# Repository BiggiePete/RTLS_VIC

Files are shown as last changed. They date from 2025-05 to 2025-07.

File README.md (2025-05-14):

# RTLS_VIC


Return to launch senior design kicad hardware repo for Vehicle In-flight Controller 

## Visit HTML BOM
https://biggiepete.github.io/RTLS_VIC/

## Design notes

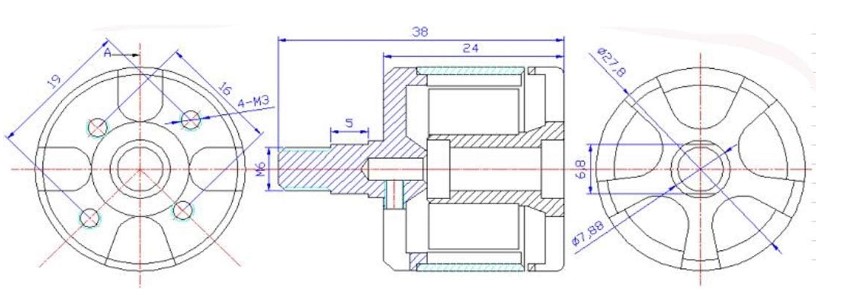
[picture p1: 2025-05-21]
motorSizing.jpg

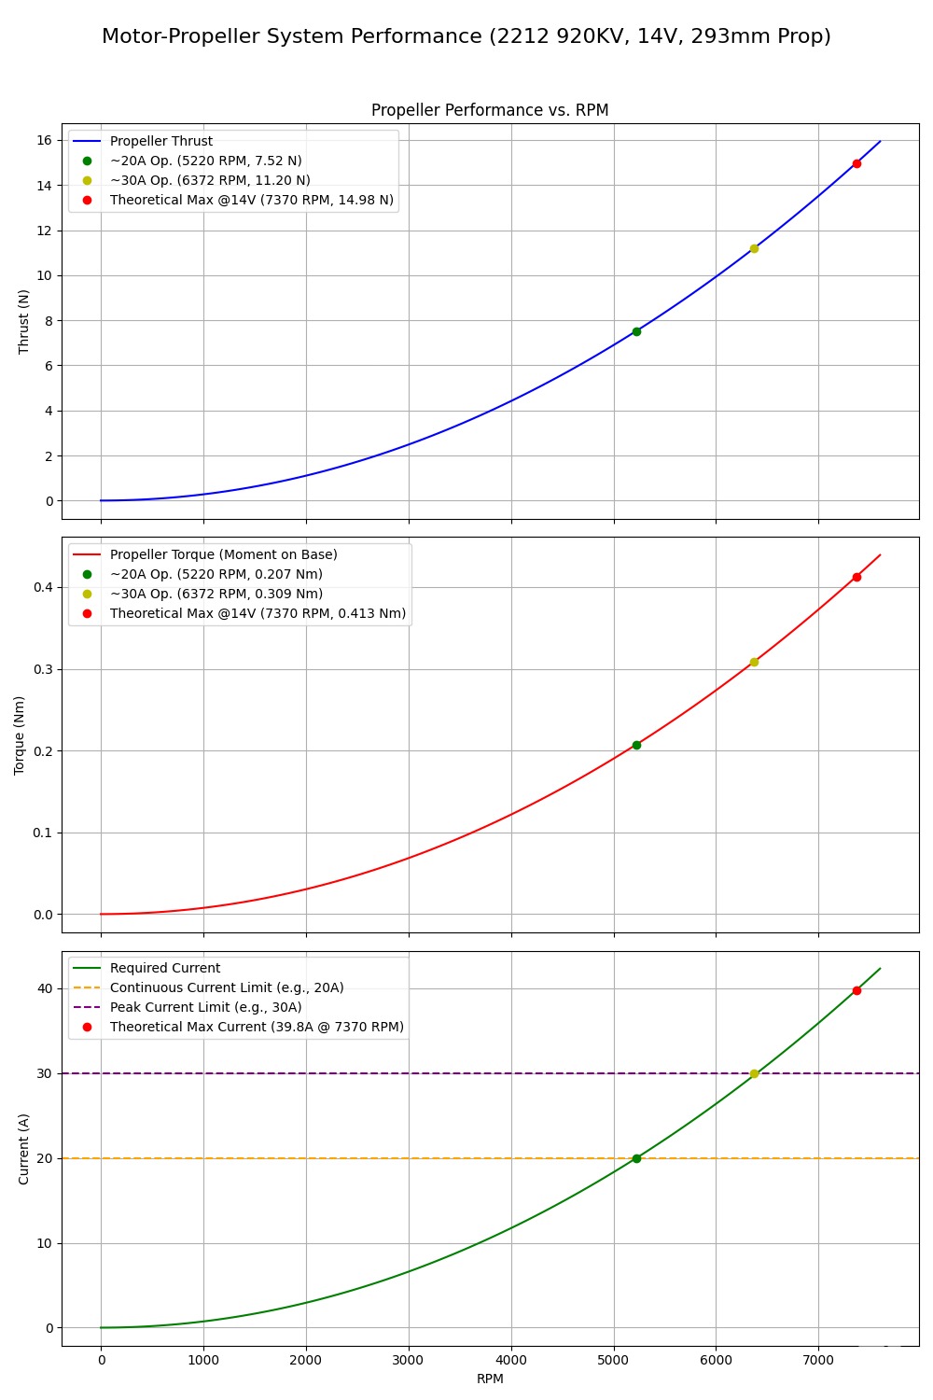
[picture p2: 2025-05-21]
CAD/sim.jpg

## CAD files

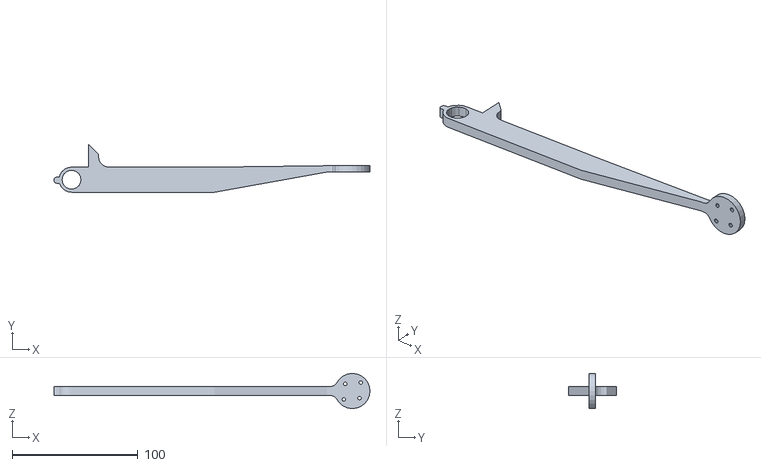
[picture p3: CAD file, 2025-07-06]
CAD/BOOM ARM.stl
251.1 x 37.8 x 28.0

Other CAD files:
CAD/OldVersions/BOOM ARM.0001.dwg
CAD/10x15x4 bearing.ipt
CAD/BOOM ARM.dwg
CAD/BOOM ARM.ipt
CAD/BOOM ASSEMBLY.iam
CAD/CENTER RING.ipt
CAD/COMPLETE ASSEMBLY.iam
CAD/MOTOR.ipt
CAD/OldVersions/BOOM ARM.0014.ipt
CAD/OldVersions/BOOM ASSEMBLY.0007.iam
CAD/OldVersions/CENTER RING.0009.ipt
CAD/OldVersions/COMPLETE ASSEMBLY.0006.iam
CAD/OldVersions/ROCKET BODY.0001.ipt
CAD/ROCKET BODY.ipt

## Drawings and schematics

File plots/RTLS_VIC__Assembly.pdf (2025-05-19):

J13 | U1 1 | 2 | 3 | 4 | 5 | 6 1 | 2 | 3 | 4 | 5 | 6 ABCD | ABCD Date: KiCad | E.D.A. 8.0.5 Size: A4 | Rev:

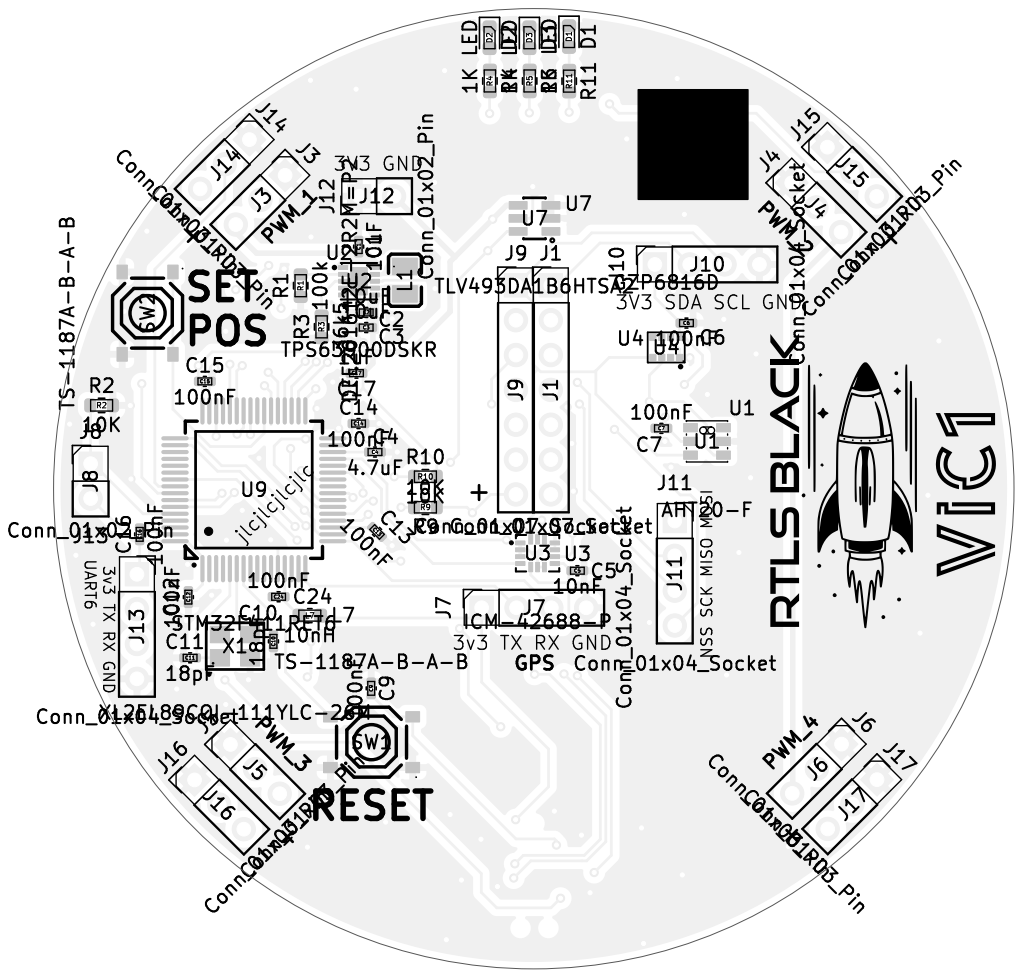
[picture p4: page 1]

A

A

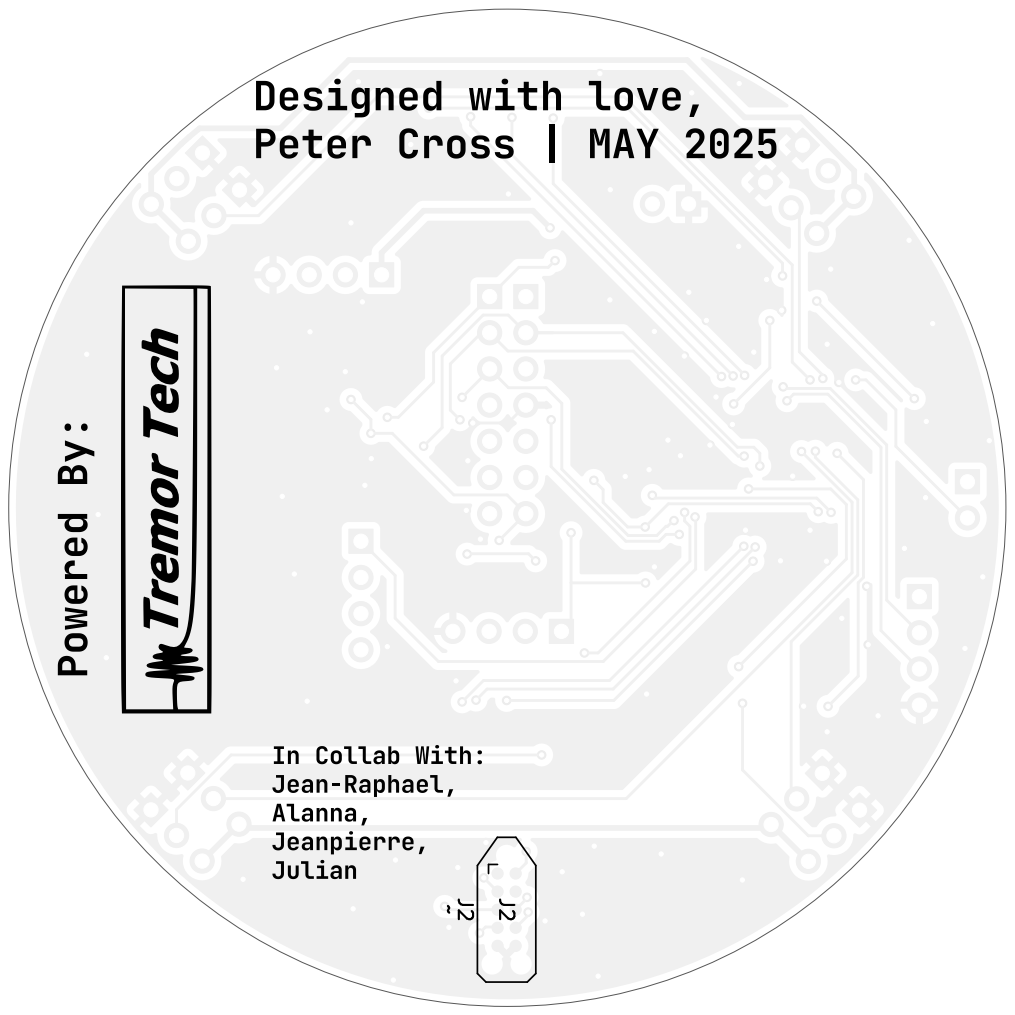
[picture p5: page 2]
Peter Cross; MAY 2025 Powered By:; In Collab With: Jean-Raphael, Alanna, Jeanpierre, Julian; D Date: KiCad; E.D.A. 8.0.5 Size: A4; Rev:; Id: 1/1 Title: File: RTLS_VIC.kicad_pcb Sheet: Black; And; White; BOT Board2Pdf:; Black; BOT -; Page 2/2

Designed with love,

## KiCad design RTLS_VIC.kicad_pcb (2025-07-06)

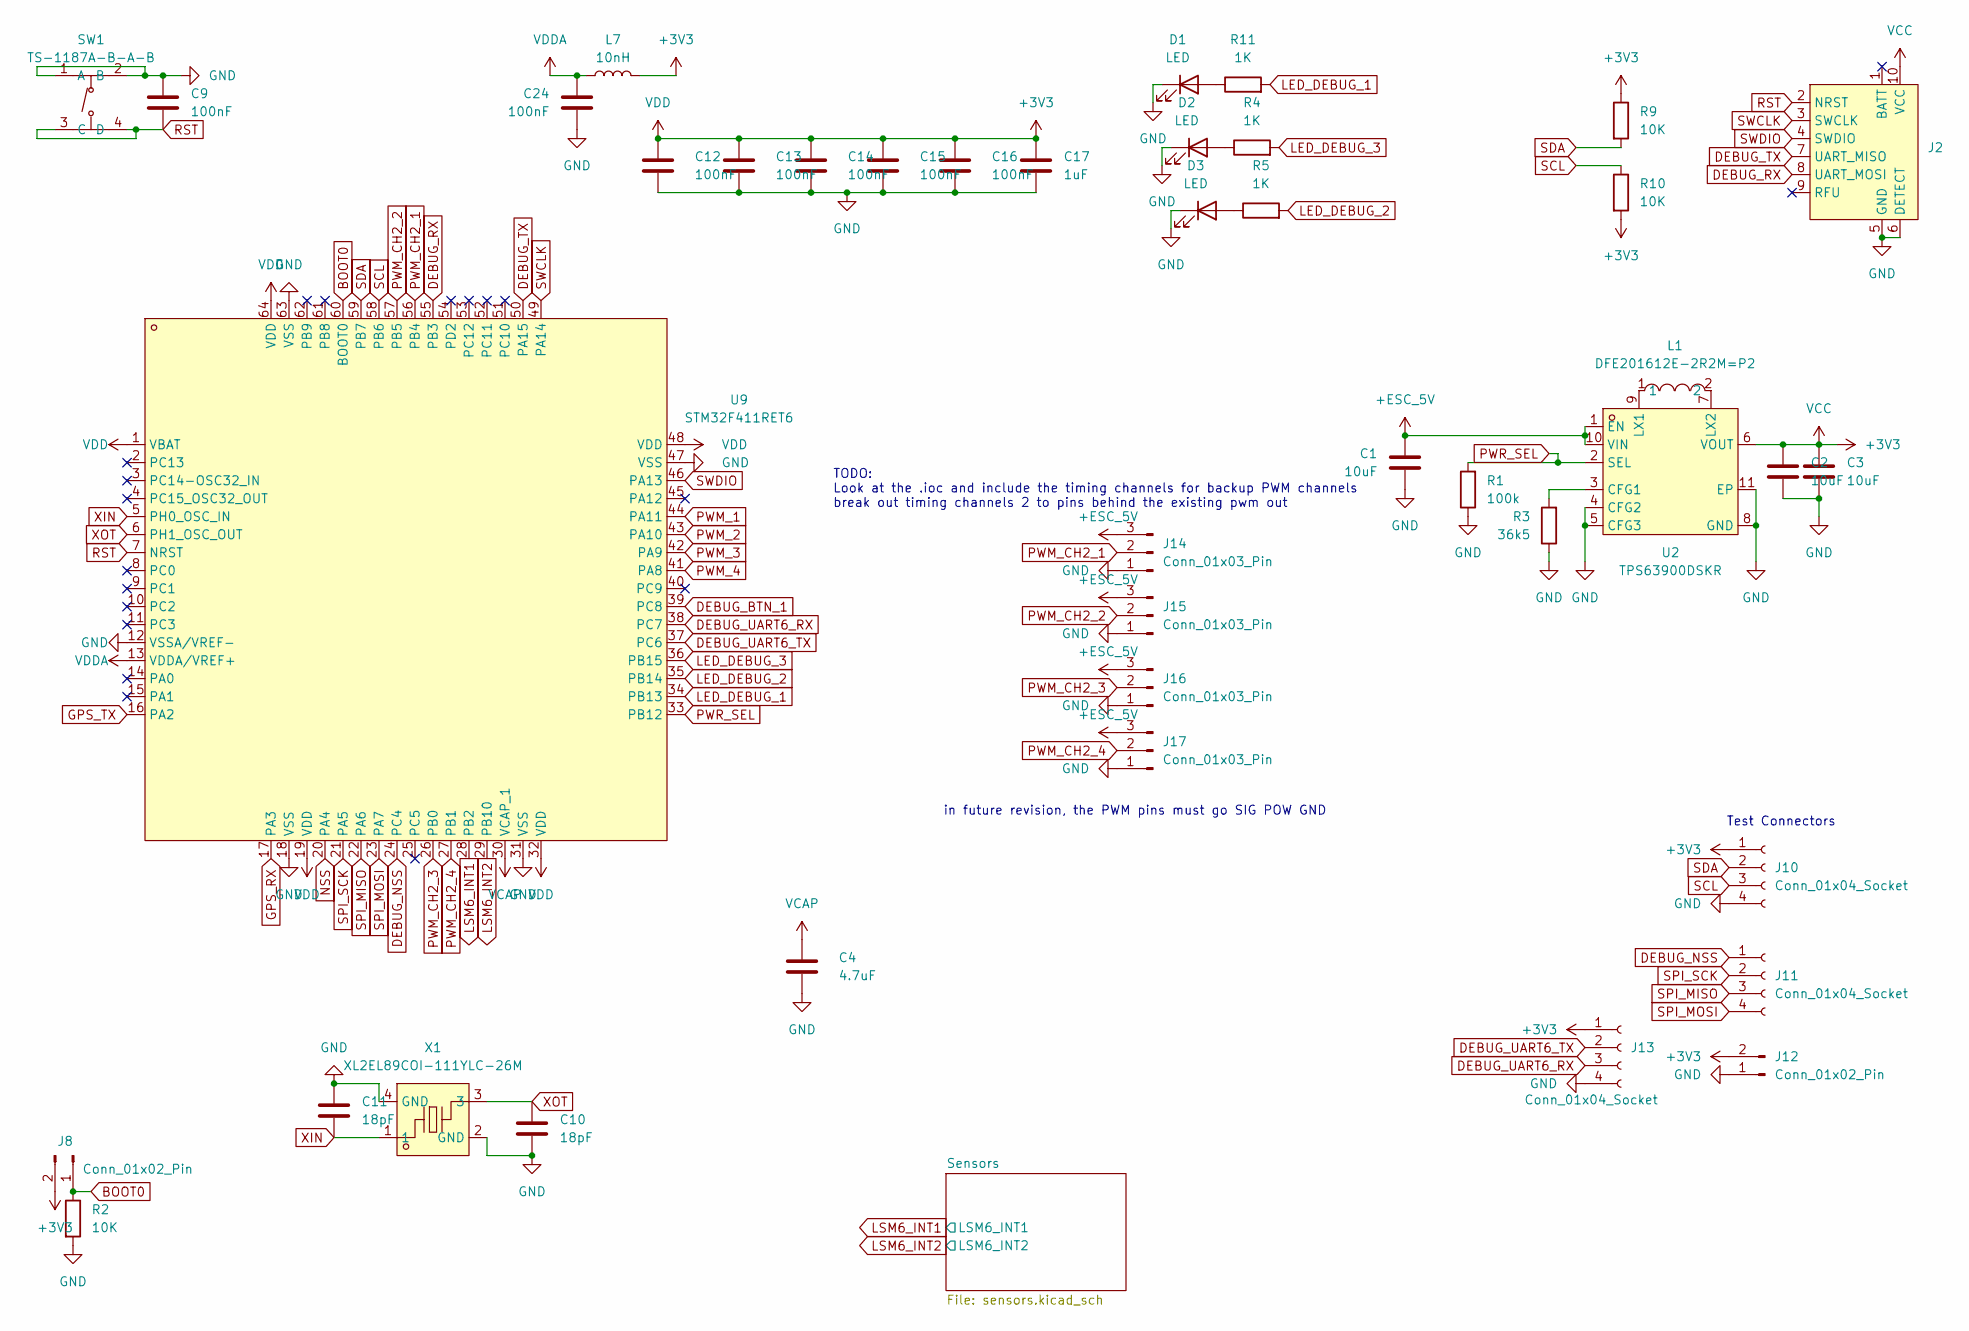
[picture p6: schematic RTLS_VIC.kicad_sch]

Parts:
C1, C2, C3: 10uF; C_0402_1005Metric; LCSC C15525
C4: 4.7uF; C_0402_1005Metric
C9, C12, C13, C14, C15, C16, C24: 100nF; C_0402_1005Metric
C10, C11: 18pF; C_0402_1005Metric
C17: 1uF; C_0402_1005Metric
D1, D2, D3: LED; LED_0603_1608Metric
J2: Tag-Connect_TC2050-IDC-NL_2x05_P1.27mm_Vertical
J8, J12: Conn_01x02_Pin; PinHeader_1x02_P2.54mm_Vertical
J10, J11, J13: Conn_01x04_Socket; PinSocket_1x04_P2.54mm_Vertical
J14, J15, J16, J17: Conn_01x03_Pin; PinHeader_1x03_P2.54mm_Vertical
L1: DFE201612E-2R2M=P2; L0806; LCSC Part C337893
L7: 10nH; L_0603_1608Metric; LCSC C913709
R1: 100k; R_0603_1608Metric; LCSC C25803
R2, R9, R10: 10K; R_0603_1608Metric
R3: 36k5; R_0603_1608Metric; LCSC C23029
R4, R5, R11: 1K; R_0603_1608Metric
SW1: TS-1187A-B-A-B; SW-SMD_4P-L5.1-W5.1-P3.70-LS6.5-TL_H1.5; LCSC Part C318884
U2: TPS63900DSKR; WSON-10_L2.5-W2.5-W0.50-TL-EP; LCSC Part C1518762
U9: STM32F411RET6; LQFP-64_L10.0-W10.0-P0.50-LS12.0-BL; LCSC Part C94355
X1: XL2EL89COI-111YLC-26M; CRYSTAL-SMD_4P-L3.2-W2.5-BL_SIT8008BI; LCSC Part C5444607

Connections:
+3V3: C2.1, C3.1, C12.1, C13.1, C14.1, C15.1, C16.1, C17.1, J2.10 (VCC), J8.2, J10.1, J12.2, J13.1, L7.2, R9.1, R10.2, U2.6 (VOUT), U9.1 (VBAT), U9.19 (VDD), U9.32 (VDD), U9.48 (VDD), U9.64 (VDD); also elsewhere on the board
+ESC_5V: C1.1, J14.3, J15.3, J16.3, J17.3, U2.1 (EN), U2.10 (VIN); also elsewhere on the board
BOOT0: J8.1, R2.1, U9.60 (BOOT0)
DEBUG_BTN_1: U9.39 (PC8); also elsewhere on the board
DEBUG_NSS: J11.1, U9.24 (PC4)
DEBUG_RX: J2.8 (UART_MOSI), U9.55 (PB3)
DEBUG_TX: J2.7 (UART_MISO), U9.50 (PA15)
DEBUG_UART6_RX: J13.3, U9.38 (PC7)
DEBUG_UART6_TX: J13.2, U9.37 (PC6)
GND: C1.2, C2.2, C3.2, C4.2, C9.1, C10.2, C11.1, C12.2, C13.2, C14.2, C15.2, C16.2, C17.2, C24.2, D1.1 (K), D2.1 (K), D3.1 (K), J2.5 (GND), J2.6 (DETECT), J10.4, J12.1, J13.4, J14.1, J15.1, J16.1, J17.1, R1.1, R2.2, R3.1, SW1.1 (A), SW1.2 (B), U2.4 (CFG2), U2.5 (CFG3), U2.8 (GND), U2.11 (EP), U9.12 (VSSA/VREF-), U9.18 (VSS), U9.31 (VSS), U9.47 (VSS), U9.63 (VSS), X1.2 (GND), X1.4 (GND); also elsewhere on the board
GPS_RX: U9.17 (PA3); also elsewhere on the board
GPS_TX: U9.16 (PA2); also elsewhere on the board
LED_DEBUG_1: R11.2, U9.34 (PB13)
LED_DEBUG_2: R5.2, U9.35 (PB14)
LED_DEBUG_3: R4.2, U9.36 (PB15)
LSM6_INT1: U9.28 (PB2); also elsewhere on the board
LSM6_INT2: U9.29 (PB10); also elsewhere on the board
NSS: U9.20 (PA4); also elsewhere on the board
unnamed: D1.2 (A), R11.1
unnamed: D2.2 (A), R4.1
unnamed: D3.2 (A), R5.1
unnamed: R3.2, U2.3 (CFG1)
unnamed: L1.1, U2.9 (LX1)
unnamed: L1.2, U2.7 (LX2)
PWM_1: U9.44 (PA11); also elsewhere on the board
PWM_2: U9.43 (PA10); also elsewhere on the board
PWM_3: U9.42 (PA9); also elsewhere on the board
PWM_4: U9.41 (PA8); also elsewhere on the board
PWM_CH2_1: J14.2, U9.56 (PB4)
PWM_CH2_2: J15.2, U9.57 (PB5)
PWM_CH2_3: J16.2, U9.26 (PB0)
PWM_CH2_4: J17.2, U9.27 (PB1)
PWR_SEL: R1.2, U2.2 (SEL), U9.33 (PB12)
RST: C9.2, J2.2 (NRST), SW1.3 (C), SW1.4 (D), U9.7 (NRST)
SCL: J10.3, R10.1, U9.58 (PB6); also elsewhere on the board
SDA: J10.2, R9.2, U9.59 (PB7); also elsewhere on the board
SPI_MISO: J11.3, U9.22 (PA6); also elsewhere on the board
SPI_MOSI: J11.4, U9.23 (PA7); also elsewhere on the board
SPI_SCK: J11.2, U9.21 (PA5); also elsewhere on the board
SWCLK: J2.3 (SWCLK), U9.49 (PA14)
SWDIO: J2.4 (SWDIO), U9.46 (PA13)
VCAP: C4.1, U9.30 (VCAP_1)
VDDA: C24.1, L7.1, U9.13 (VDDA/VREF+)
XIN: C11.2, U9.5 (PH0_OSC_IN), X1.1
XOT: C10.1, U9.6 (PH1_OSC_OUT), X1.3

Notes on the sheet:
TODO: Look at the .ioc and include the timing channels for backup PWM channels break out timing channels 2 to pins behind the existing pwm out
Test Connectors
in future revision, the PWM pins must go SIG POW GND

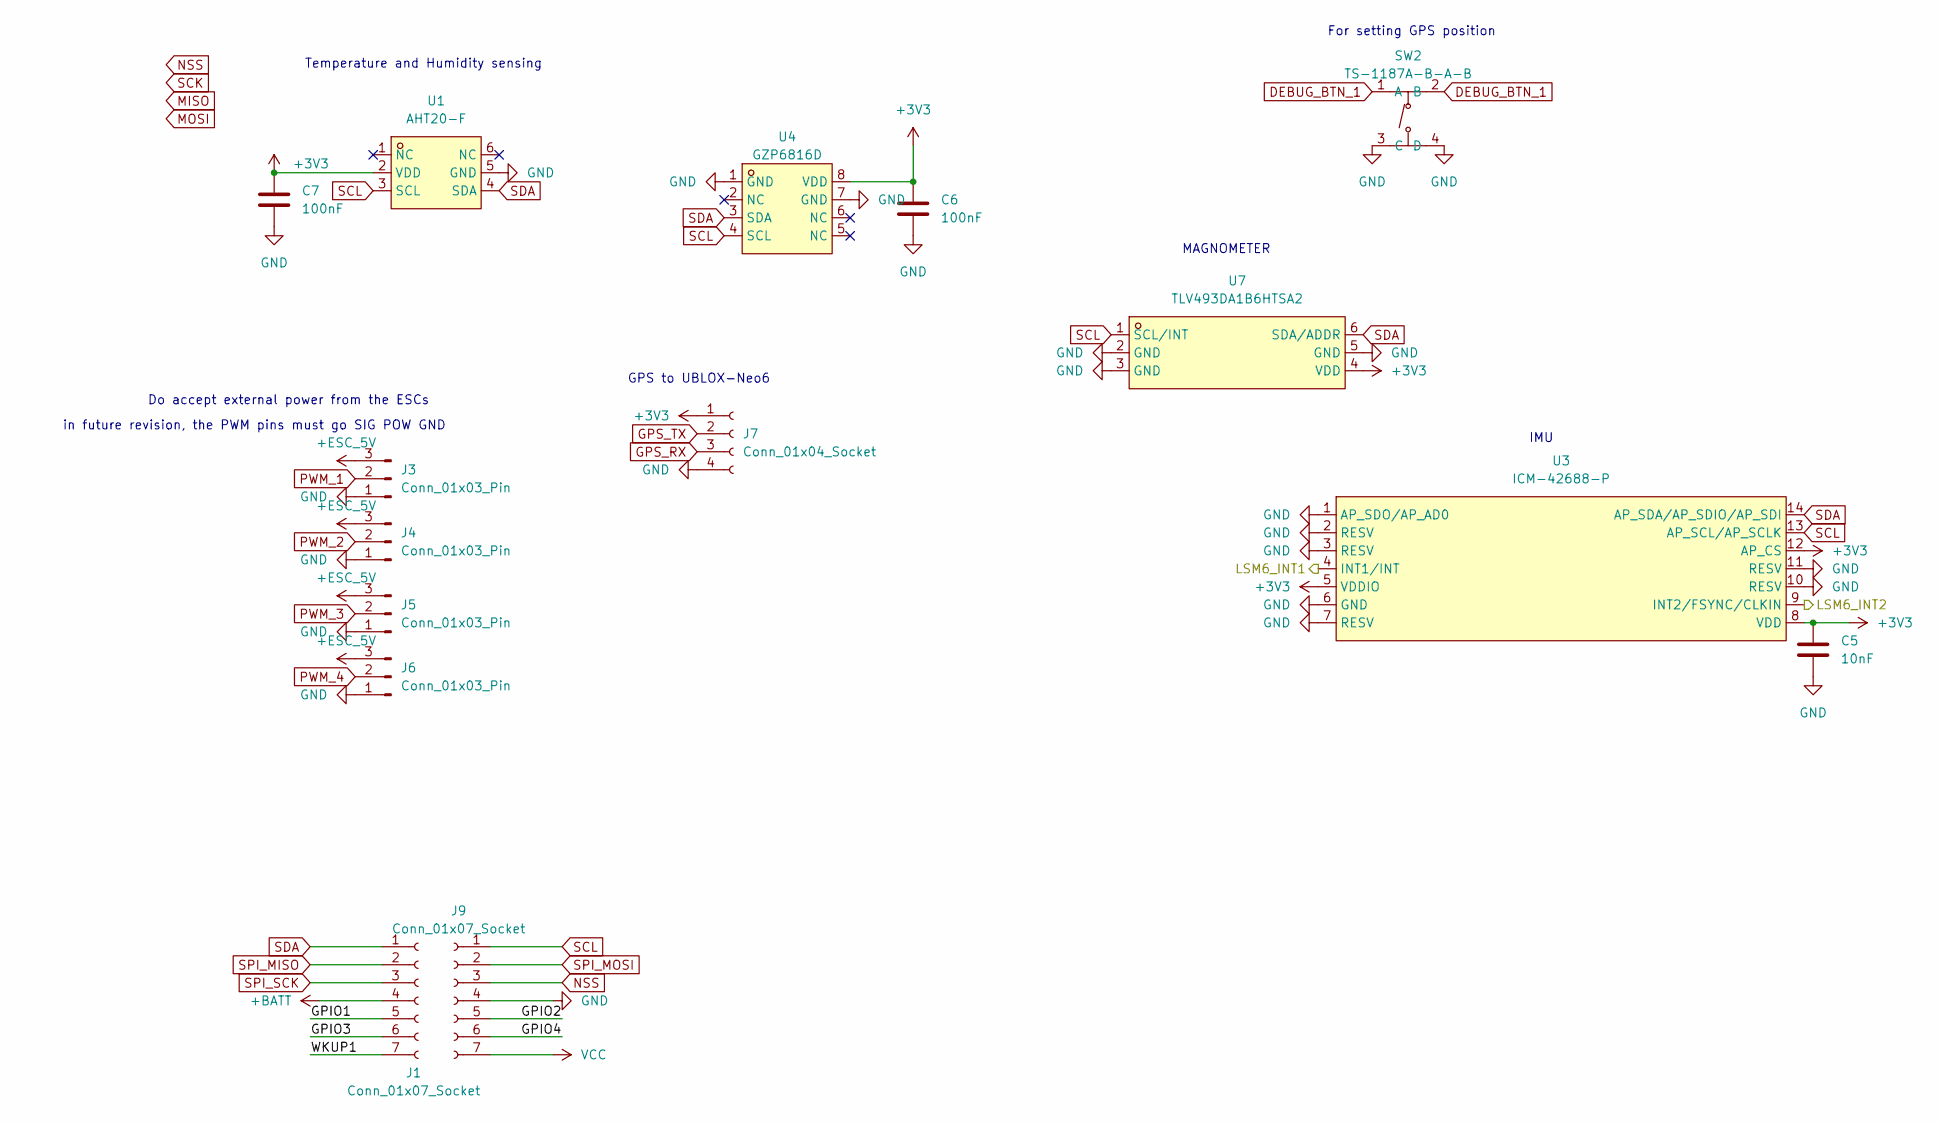
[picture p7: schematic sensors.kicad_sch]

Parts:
C5: 10nF; C_0402_1005Metric
C6, C7: 100nF; C_0402_1005Metric
J1, J9: Conn_01x07_Socket; PinHeader_1x07_P2.54mm_Vertical
J3, J4, J5, J6: Conn_01x03_Pin; PinHeader_1x03_P2.54mm_Vertical
J7: Conn_01x04_Socket; PinSocket_1x04_P2.54mm_Vertical
SW2: TS-1187A-B-A-B; SW-SMD_4P-L5.1-W5.1-P3.70-LS6.5-TL_H1.5; LCSC Part C318884
U1: AHT20-F; SENSOR-SMD-6_AHT20; LCSC Part C3012622
U3: ICM-42688-P; LGA-14_L3.0-W2.5-P0.50-TL; LCSC Part C1850418
U4: GZP6816D; SENSOR-SMD_XGZP6816D; LCSC Part C3038127
U7: TLV493DA1B6HTSA2; SOP-6_L3.0-W1.5-P0.95-LS2.5-BR; LCSC Part C126688

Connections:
+3V3: C5.1, C6.1, C7.1, J7.1, J9.7, U1.2 (VDD), U3.5 (VDDIO), U3.8 (VDD), U3.12 (AP_CS), U4.8 (VDD), U7.4 (VDD); also elsewhere on the board
+BATT: J1.4
+ESC_5V: J3.3, J4.3, J5.3, J6.3; also elsewhere on the board
/Sensors/GPIO1: J1.5
/Sensors/GPIO2: J9.5
/Sensors/GPIO3: J1.6
/Sensors/GPIO4: J9.6
/Sensors/WKUP1: J1.7
DEBUG_BTN_1: SW2.1 (A), SW2.2 (B); also elsewhere on the board
GND: C5.2, C6.2, C7.2, J3.1, J4.1, J5.1, J6.1, J7.4, J9.4, SW2.3 (C), SW2.4 (D), U1.5 (GND), U3.1 (AP_SDO/AP_AD0), U3.2 (RESV), U3.3 (RESV), U3.6 (GND), U3.7 (RESV), U3.10 (RESV), U3.11 (RESV), U4.1 (GND), U4.7 (GND), U7.2 (GND), U7.3 (GND), U7.5 (GND); also elsewhere on the board
GPS_RX: J7.3; also elsewhere on the board
GPS_TX: J7.2; also elsewhere on the board
LSM6_INT1: U3.4 (INT1/INT); also elsewhere on the board
LSM6_INT2: U3.9 (INT2/FSYNC/CLKIN); also elsewhere on the board
NSS: J9.3; also elsewhere on the board
PWM_1: J3.2; also elsewhere on the board
PWM_2: J4.2; also elsewhere on the board
PWM_3: J5.2; also elsewhere on the board
PWM_4: J6.2; also elsewhere on the board
SCL: J9.1, U1.3 (SCL), U3.13 (AP_SCL/AP_SCLK), U4.4 (SCL), U7.1 (SCL/INT); also elsewhere on the board
SDA: J1.1, U1.4 (SDA), U3.14 (AP_SDA/AP_SDIO/AP_SDI), U4.3 (SDA), U7.6 (SDA/ADDR); also elsewhere on the board
SPI_MISO: J1.2; also elsewhere on the board
SPI_MOSI: J9.2; also elsewhere on the board
SPI_SCK: J1.3; also elsewhere on the board

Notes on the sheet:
in future revision, the PWM pins must go SIG POW GND
MAGNOMETER
GPS to UBLOX-Neo6
IMU
Do accept external power from the ESCs
For setting GPS position
Temperature and Humidity sensing

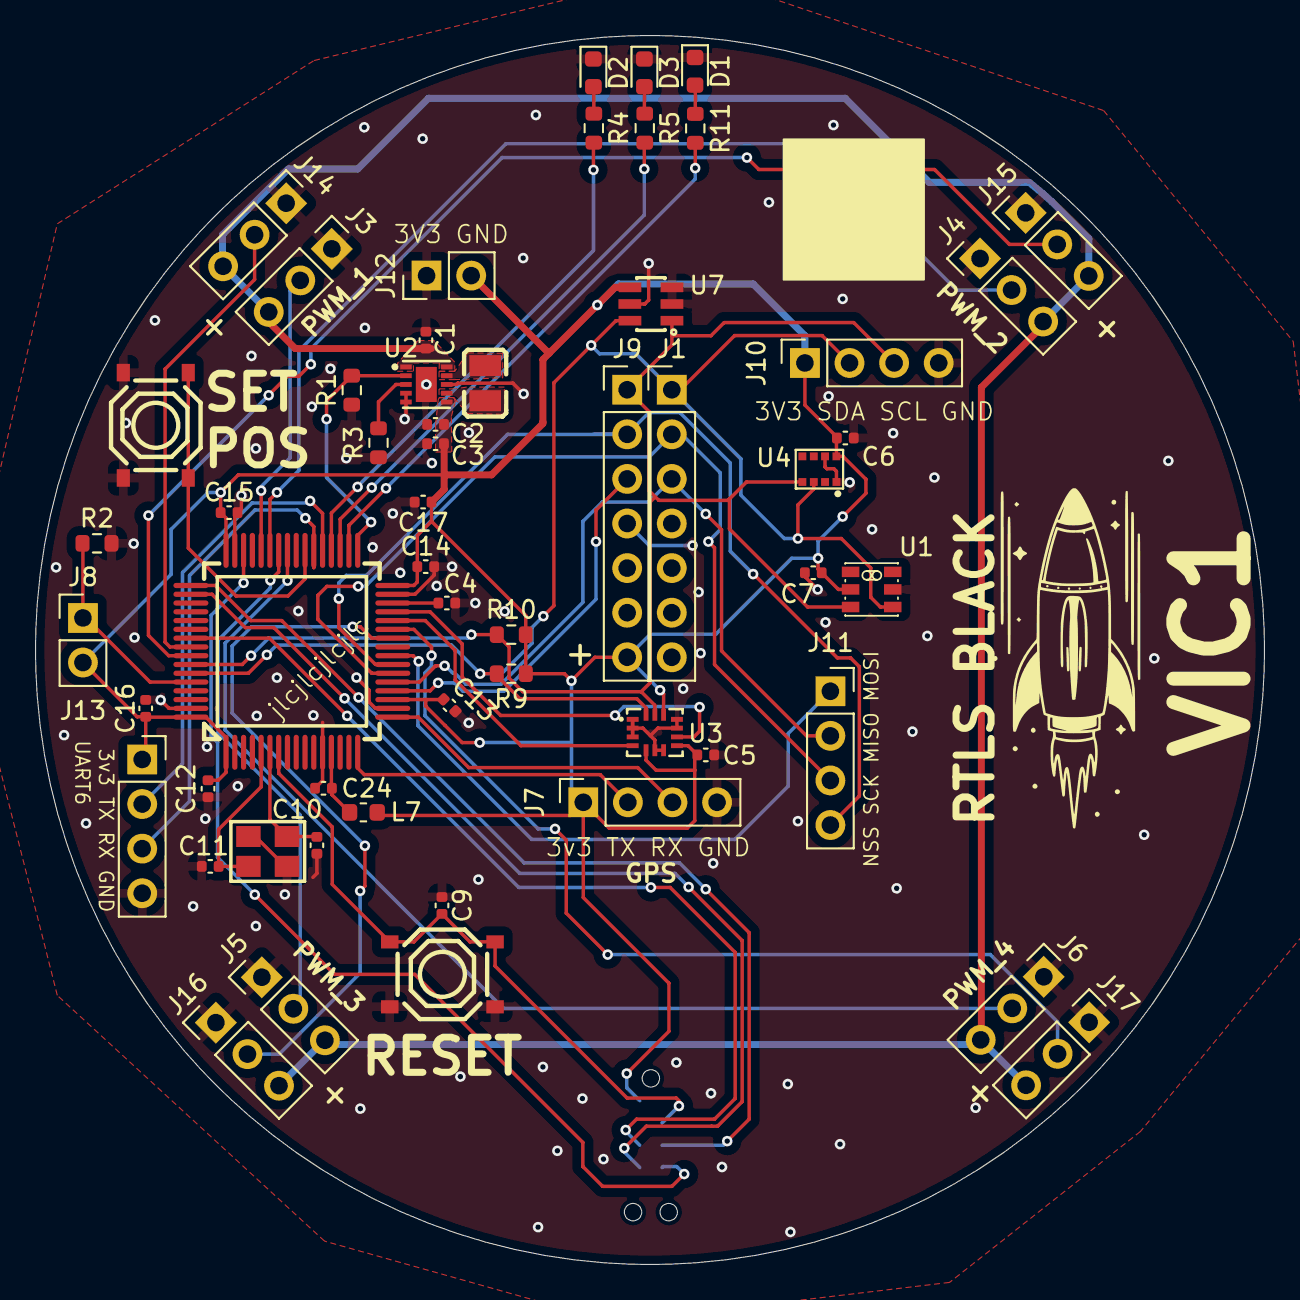
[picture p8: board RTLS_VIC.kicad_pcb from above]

Board: 2 copper layers, 70.0 x 70.0 mm, 56 parts (1 on the bottom side), 45 nets.

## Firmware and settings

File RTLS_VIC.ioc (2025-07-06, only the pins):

Mcu.UserName=STM32F411RETx
PA10.Signal=S_TIM1_CH3
PA11.Signal=S_TIM1_CH4
PA13.Signal=SYS_JTMS-SWDIO
PA14.Signal=SYS_JTCK-SWCLK
PA15.Signal=USART1_TX
PA2.Signal=USART2_TX
PA3.Signal=USART2_RX
PA5.Signal=SPI1_SCK
PA6.Signal=SPI1_MISO
PA7.Signal=SPI1_MOSI
PA8.Signal=S_TIM1_CH1
PA9.Signal=S_TIM1_CH2
PB0.Signal=S_TIM3_CH3
PB1.Signal=S_TIM3_CH4
PB3.Signal=USART1_RX
PB4.Signal=S_TIM3_CH1
PB5.Signal=S_TIM3_CH2
PB6.Signal=I2C1_SCL
PB7.Signal=I2C1_SDA
PC6.Signal=USART6_TX
PC7.Signal=USART6_RX

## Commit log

2025-04-18 getting somewhere
    [RTLS_VIC.kicad_pcb, RTLS_VIC.kicad_sch, radio.kicad_sch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]
2025-04-26 add notes
    [RTLS_VIC.kicad_sch, radio.kicad_sch, sensors.kicad_sch]
2025-05-12 major overhaul
    [RTLS_VIC.kicad_pcb, RTLS_VIC.kicad_sch, sensors.kicad_sch]
2025-05-13 html bom
    [RTLS_VIC.kicad_pcb]
2025-05-14 list bom dir
2025-05-14 working on placements
    [RTLS_VIC.kicad_pcb, RTLS_VIC.kicad_sch, sensors.kicad_sch]
2025-05-15 nearly there
    [RTLS_VIC.kicad_pcb, RTLS_VIC.kicad_sch, sensors.kicad_sch]
2025-05-16 preparing for prod
    [RTLS_VIC-CuBottom.gbr, RTLS_VIC-CuTop.gbr, RTLS_VIC-EdgeCuts.gbr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]
2025-05-16 build bom
    [RTLS_VIC-CuBottom.gbr, RTLS_VIC-CuTop.gbr, RTLS_VIC-EdgeCuts.gbr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]
2025-05-16 one more bom gen
    [RTLS_VIC-CuBottom.gbr, RTLS_VIC-CuTop.gbr, RTLS_VIC-EdgeCuts.gbr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]
2025-05-16 forgot to do timing channel 2
    [RTLS_VIC.kicad_pcb, RTLS_VIC.kicad_sch]
2025-05-17 sponsor and timing
    [RTLS_VIC-CuBottom.gbr, RTLS_VIC-CuTop.gbr, RTLS_VIC-EdgeCuts.gbr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]
2025-05-17 fix resistor mis-sized
    [RTLS_VIC-CuBottom.gbr, RTLS_VIC-CuTop.gbr, RTLS_VIC-EdgeCuts.gbr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]
2025-05-19 fix issues with power supply
    [RTLS_VIC-CuBottom.gbr, RTLS_VIC-CuTop.gbr, RTLS_VIC-EdgeCuts.gbr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]
2025-05-19 add measurement
    [RTLS_VIC.kicad_pcb]
2025-05-21 initial boom arm cad and sim
    [BOOM ARM.0004.ipt, BOOM ARM.ipt, BOOM ASSEMBLY.0001.iam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]
2025-05-21 sim thrust math
2025-07-06 new cad models
    [10x15x4 bearing.ipt, BOOM ARM.0008.ipt, BOOM ARM.0014.ipt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]
2025-07-15 before first print
    [BOOM ASSEMBLY.0006.iam, BOOM ASSEMBLY.0007.iam, BOOM ASSEMBLY.iam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]
